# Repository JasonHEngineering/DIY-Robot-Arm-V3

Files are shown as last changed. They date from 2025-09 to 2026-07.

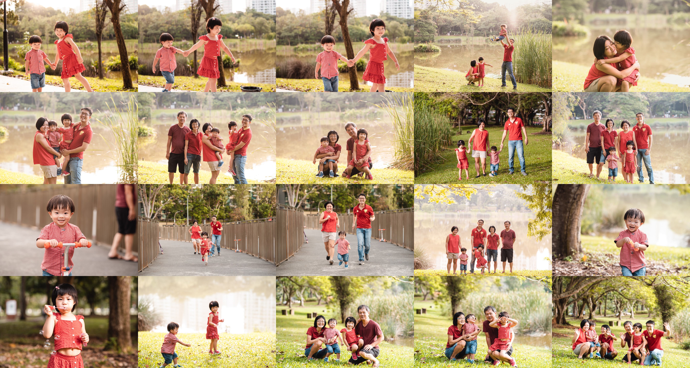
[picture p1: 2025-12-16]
Raspberry Pi - Python (Plotly dash user interface/assets/result.jpg

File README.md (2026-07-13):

# DIY-Robot-Arm-V3 

Introduction - https://youtu.be/GQhKxkShxAY

cover_page

CAD gif

# Parts Cost Estimation (SGD)

| Parts | Est. Cost (SGD) | Link |
|---|---:|---|
| CNC parts (including shipping cost) | 740 | [CAD file in GitHub](https://github.com/JasonHEngineering/DIY-Robot-Arm-V3/tree/main/CAD%20(2d%20%2B%20step%20files)) |
| 3d printed parts (including shipping cost) | 69 | [CAD file in GitHub](https://github.com/JasonHEngineering/DIY-Robot-Arm-V3/tree/main/CAD%20(2d%20%2B%20step%20files)) |
| Main PCBA (5x, including SMD assembly & shipping cost) | 158 | [Design files in GitHub](https://github.com/JasonHEngineering/DIY-Robot-Arm-V3/tree/main/PCBA%20(schema%2C%20gerbers%2C%20kicad%20project)) |
| Encoder PCBA (10x, including SMD assembly & shipping cost) | 132 | [Design files in GitHub](https://github.com/JasonHEngineering/DIY-Robot-Arm-V3/tree/main/PCBA%20(schema%2C%20gerbers%2C%20kicad%20project)) |
| Bearing 6805 2RS (25x37x7mm) (3x) | 16.07 | [AliExpress](https://s.click.aliexpress.com/e/_c33xzexj) |
| Bearing lock nut M24x1.5x30x5 (3x) | 6.24 | [AliExpress](https://s.click.aliexpress.com/e/_c3OO3rFf) |
| M3 set screw with nylon head | 4.84 | [AliExpress](https://s.click.aliexpress.com/e/_c3lDO1O5) |
| Pulley (Bore 8mm, belt width 6 mm, 2GT-30T) | 4.48 | [AliExpress](https://s.click.aliexpress.com/e/_c4LLe4XL) |
| Pulley (Bore 12mm, belt width 6 mm, 2GT-30T) | 3.06 | [AliExpress](https://s.click.aliexpress.com/e/_c3QfG9gt) |
| Timing belt (2GT-200-6mm) | 1.02 | [AliExpress](https://s.click.aliexpress.com/e/_c4KhaszX) |
| Diametric Magnets for encoders (10 pcs / lot) | 3.68 | [AliExpress](https://s.click.aliexpress.com/e/_c3Axm1QN) |
| FFC cables (pitch 0.5 mm) | 6.00 | [AliExpress](https://s.click.aliexpress.com/e/_c4SXa38p) |
| Stepper motor cables (XH2.54) | 10.00 | [AliExpress](https://s.click.aliexpress.com/e/_c3dAdb65) |
| Stepper motor 60mm model 17CS07A-180 (2x) | 38.64 | [AliExpress](https://s.click.aliexpress.com/e/_c2yzH5rf) |
| Stepper motor 60mm model 17HS4023 (3x) | 25.29 | [AliExpress](https://s.click.aliexpress.com/e/_c4bld957) |
| Stepper motor 60mm model 17HS3401S-SZ (1x) | 12.29 | [AliExpress](https://s.click.aliexpress.com/e/_c31tJidB) |
| X17-30A harmonic reducer (30:1) (5x) | 338.00 | [AliExpress](https://s.click.aliexpress.com/e/_c3xNHvpT) |
| Raspberry Pi 4B, 4GB | 160.00 | [AliExpress](https://s.click.aliexpress.com/e/_c45i6ECJ) |
| ESP32-S3-DevKitC-1 (n16r8) | 14.63 | [AliExpress](https://s.click.aliexpress.com/e/_c41bdQlh) |
| Pins & connectors (22 pins) | 1.91 | [AliExpress](https://s.click.aliexpress.com/e/_c3fCAogH) |
| TMC2209 V1.3 motor drivers (6x) | 24.13 | [AliExpress](https://s.click.aliexpress.com/e/_c4b6KFWH) |
| 24V fan (60x60x15mm) | 2.89 | [AliExpress](https://s.click.aliexpress.com/e/_c3T1QZcp) |
| E-Stop Button | 4.15 | [AliExpress](https://s.click.aliexpress.com/e/_c3gcdvel) |
| DOIT ESP32 DEV KIT V1 | 7.27 | [AliExpress](https://s.click.aliexpress.com/e/_c3el80wp) |
| PS controller | 13.34 | [AliExpress](https://s.click.aliexpress.com/e/_c4OqUEGd) |
| Mini-560-Pro (Mini Pro 5V, 3A for Raspberry Pi) | 1.51 | [AliExpress](https://s.click.aliexpress.com/e/_c37WkxiV) |
| Optical Experiment Plate 5052 Aluminum 280x320x8mm | 71.25 | [AliExpress](https://s.click.aliexpress.com/e/_c3tvnmLj) |
| Servo Claw | 26.26 | [AliExpress](https://s.click.aliexpress.com/e/_c3I3E3Mh) |
| Servo motor MG996R | 6.74 | [AliExpress](https://s.click.aliexpress.com/e/_c3sTutbP) |
| Standoffs, clamps, dowel pins | 10.00 | |
| Fasteners | 10.00 | |

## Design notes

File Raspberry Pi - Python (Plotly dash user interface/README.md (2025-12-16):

# User Interface hosted in Raspberry Pi 3/4 (Work in progress)

Plotly Dash App - written in Python. 3 main pages.

Page 1 - "Angles"
To control robotic arm by angle entries.



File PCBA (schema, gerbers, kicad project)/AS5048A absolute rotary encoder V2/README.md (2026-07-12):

# Notes 

1) Although there are 7 jumper pads here for purpose of using these encoders in series with SPI protocol, however due to GPIO0 on ESP32-S3 being a bootstrap pin, I will not be using jumper JP5 on the absolute encoder board at all. Consequently, the remaining chip select jumper for all the 6 axis encoders are allocated as shown in the table, with the soldering done accordingly.

<!-- wp:image {"id":4006,"sizeSlug":"large","linkDestination":"none"} -->

<!-- /wp:image -->

<!-- wp:image {"id":4002,"sizeSlug":"large","linkDestination":"none"} -->

<!-- /wp:image -->

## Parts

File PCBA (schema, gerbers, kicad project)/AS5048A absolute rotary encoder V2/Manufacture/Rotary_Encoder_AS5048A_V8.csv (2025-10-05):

Comment | Designator | Footprint | LCSC
GRM155R60J106ME15D | C1 | 10uF_cap_GRM155R60J106ME15D:CAPC1005X65N | C412251
GCM155R71C104KA55J | C2 | 100nf_cap_GCM155R71C104KA55J:CAPC1005X55N | C2655418
CC0603KRX7R7BB105 | C3,C4 | MLCC_16V_1uF_X7R_±10%_0603_C106248:MLCC_16V_1uF_X7R_±10%_0603_C106248 | C106248
BAT20JFILM | D1 | diode_BAT20JFILM:SOD-323 | C155590
AFC01-S12FCA-00 | FPC1,FPC2 | FFC_conn_Flip type_12P_P=0.5mm_C262661:FFC_conn_Flip type_12P_P=0.5mm_C262661 | C262661
Conn_01x01_Female | J2 | Connector_PinHeader_1.00mm:PinHeader_1x01_P1.00mm_Vertical
Jumper_2_Open | JP1,JP2,JP3,JP4,JP5,JP6,JP7 | solder_jumpers:SolderJumper-2_P1.3mm_Open_TrianglePad1.0x1.5mm
Green | LED1 | green_LED_wurth_150060GS75000_0603_C5252984:LEDC1608X80N | C5252984
0402WGD1001TCE | R1 | Resistor_62.5mW_50V_±0.5%_1kΩ_0402_C407754:Resistor_62.5mW_50V_±0.5%_1kΩ_0402_C407754 | C407754
RC0402FR-0733RL | R2 | Resistor_62.5mW_50V_±1%_33Ω_0402_C138002:Resistor_62.5mW_50V_±1%_33Ω_0402_C138002 | C138002
RC0402FR-0710KL | R3 | Resistor_62.5mW_50V_±1%_10kΩ_0402_C60490:Resistor_62.5mW_50V_±1%_10kΩ_0402_C60490 | C60490
AS5048A | U1 | Package_SO:TSSOP-14_4.4x5mm_P0.65mm | C2655181
TLV75733PDBVR | U2 | LDO_1A_Fixed_3.3V_out_5.5V_in_SOT-23-5_C485517:LDO_1A_Fixed_3.3V_out_5.5V_in_SOT-23-5_C485517 | C485517

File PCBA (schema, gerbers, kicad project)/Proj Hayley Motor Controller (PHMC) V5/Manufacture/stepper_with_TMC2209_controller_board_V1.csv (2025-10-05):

Comment | Designator | Footprint | LCSC
FS55X226K500EHG | C1,C6 | Cap_MLCC_50V_22uF_X7R_2220_C784103:Cap_MLCC_50V_22uF_X7R_2220_C784103 | C784103
CC0603KRX7R9BB104 | C2 | MLCC_Yageo_50V_100nF_X7R_±10%_0603_C14663:MLCC_Yageo_50V_100nF_X7R_±10%_0603_C14663 | C14663
470uF, 35V | C3 | 470uF_35V_Alu_cap_panasonic_EEH-ZS1V471P_C403803:CAP_EEHZS1V471P | C403803
GCM155R71C104KA55J | C4 | 100nf_cap_GCM155R71C104KA55J:CAPC1005X55N | C2655418
0.1uF, 16V | C5 | 100nf_16V_MLCC_GRM155R71C104KA88D_C71629:CAPC1005X55N | C71629
CGA2B3X7R1V104KT0Y0F | C7,C8,C11,C12,C15,C16,C19,C20 | TDK cap_100nF_35V_C0402_C343047:C0402_L1.0-W0.5-H0.5 | C343047
RVT1V101M0605 | C9,C10,C13,C14,C17,C18 | Capacitor_100uF_35V_75mA@120Hz_±20%_D6pt3xL5pt4mm_C3151830:Capacitor_100uF_35V_75mA@120Hz_±20%_D6pt3xL5pt4mm_C3151830 | C3151830
BZT52C5V6S_C19077441 | D2 | BZT52C5V6S_5.2V_to_6V_200mW_5.6V_SOD-323_Zener_Diodes_C19077441:SOD-323_L1.7-W1.3-LS2.6-RD | C19077441
0ZCJ0020FF2E | F1 | Bel_Fuse_0ZCJ0020FF2E_30V_200mA_10A_400mA_1206_Resettable_Fuses_C6964258.pretty:F1206 | C6964258
AFC01-S12FCA-00 | FPC1 | FFC_conn_Flip type_12P_P=0.5mm_C262661:FFC_conn_Flip type_12P_P=0.5mm_C262661 | C262661
FTC252012S100MBCA | L1 | Inductor_10uH_1pt6A_2x2pt5mm_C5832376:Inductor_10uH_1pt6A_2x2pt5mm_C5832376 | C5832376
Green | LED1 | green_LED_wurth_150060GS75000_0603_C5252984:LEDC1608X80N | C5252984
MAC97A8-23-3L | Q1 | KY_MAC97A8-23-3L_10mA_800V_SOT-23-3L_Thyristors_SCR_C2831929:SOT-23-3_L2.9-W1.6-P1.90-LS2.8-BL-A | C2831929
5kR, 0.25W | R1,R33,R34 | 5kR_250mW_yageo_RT1206BRD075KL_1206_C870818:RESC3116X65N | C870818
10kR, 100mW | R2 | 10kR_100mW_yageo_RC0603FR-0710KL_0603_C98220:RESC1607X60N | C98220
1kR, 0.25W | R20,R21 | 1kR_250mW_yageo_RC1206FR-071KL_1206_C131398:RESC3116X65N | C131398
RC0402FR-07100KL | R3,R4,R8,R15,R16,R17,R18,R19 | Resistor_ 100kΩ_62.5mW_50V_0402_C60491:Resistor_ 100kΩ_62.5mW_50V_0402_C60491 | C60491
FRC0805F1902TS | R5 | Resistor_19kΩ_0.125W_150V_0805_C2930177:Resistor_19kΩ_0.125W_150V_0805_C2930177 | C2930177
33R, 0.1W | R6,R7,R26,R27,R28,R29,R30,R31,R32 | 33R_100mW_yageo_RC0603JR-0733RL_0603_C108407:RESC1608X55N | C108407
0402WGF2000TCE | R9,R10,R11,R12,R13,R14 | 62.5mW_Resistor_50V_±1%_200Ω_0402_C25087:R0402 | C25087
DSWB06LHGET | SW1 | 6_SPST_Through_Hole_DIP_C99416:6_SPST_Through_Hole_DIP_C99416 | C99416
TP6841S6-A | U1 | Step-down_800mA_4.5V_to_40V_SOT-23-6_C2844924:SOT-23-6_L2.9-W1.6-P0.95-LS2.8-BL | C2844924
XL-1608UBC-06A | U2,U5,U6,U7,U8,U9,U10 | Blue_LED_5mA_456nm~476nm_130°_2.6V~3V_0603_C7371904:Blue_LED_5mA_456nm~476nm_130°_2.6V~3V_0603_C7371904 | C7371904
XT30UPB-M | U4 | high_current_connector_amass_XT30UPB-M_C108769:XT30UPB-M | C108769

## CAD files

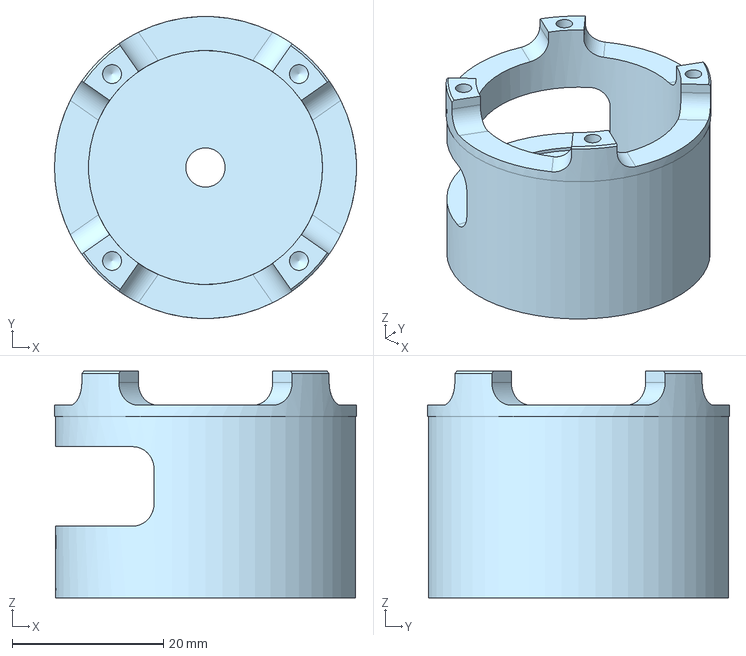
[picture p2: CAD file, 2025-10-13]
CAD (2d + step files)/Step Files/Part Studio 51.step
40.0 x 40.0 x 30.0 mm

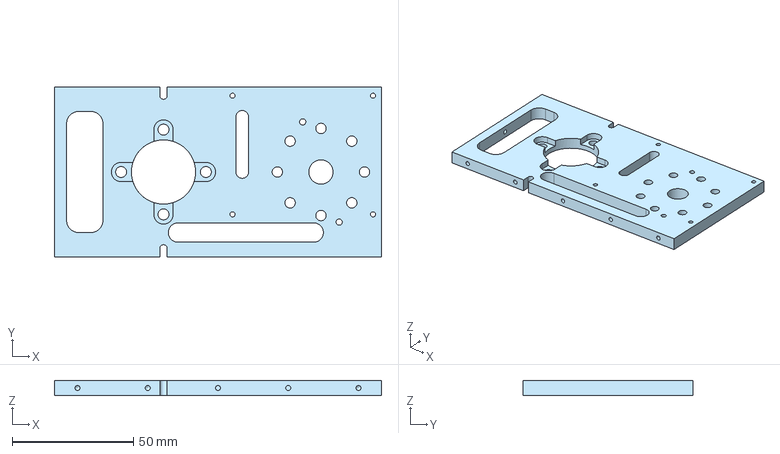
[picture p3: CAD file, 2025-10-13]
CAD (2d + step files)/Step Files/Part Studio 52.step
135.0 x 70.0 x 6.00 mm

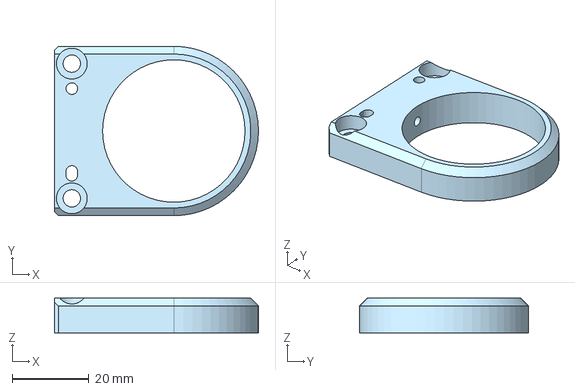
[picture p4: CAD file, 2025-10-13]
CAD (2d + step files)/Step Files/Part Studio 42.step
53.0 x 44.0 x 9.00 mm

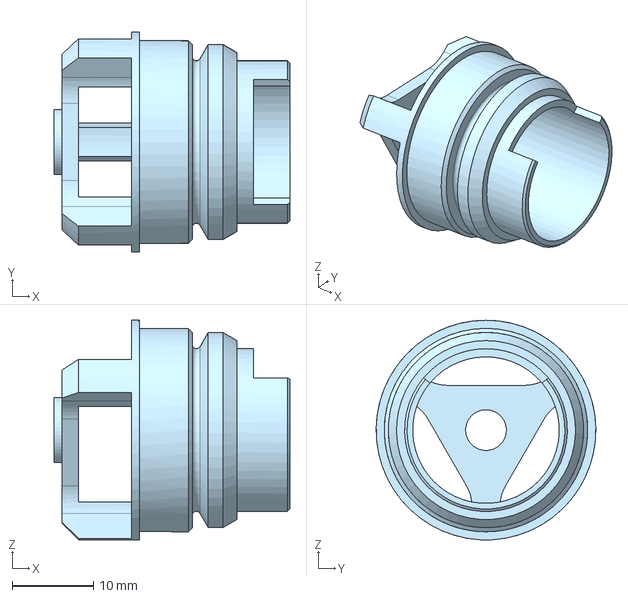
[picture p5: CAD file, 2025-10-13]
CAD (2d + step files)/Step Files/Part Studio 29.step
29.0 x 27.0 x 27.0 mm

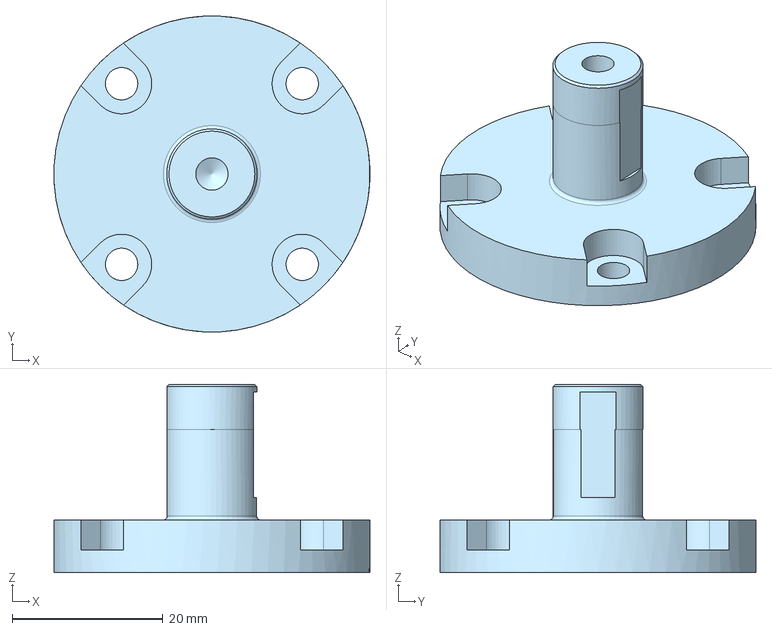
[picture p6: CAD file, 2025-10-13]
CAD (2d + step files)/Step Files/Part Studio 49.step
42.0 x 42.0 x 25.0 mm

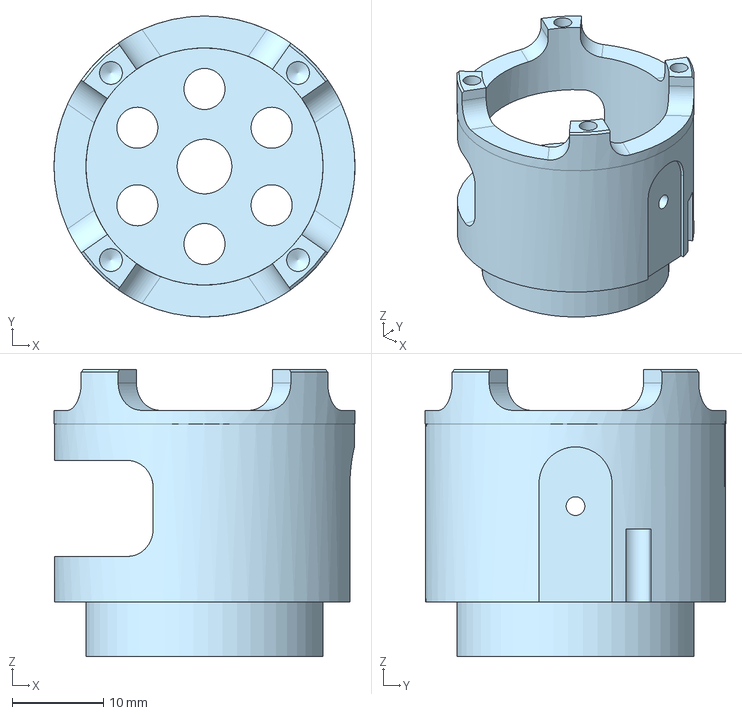
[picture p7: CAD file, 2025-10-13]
CAD (2d + step files)/Step Files/Part Studio 36.step
33.0 x 33.0 x 31.5 mm

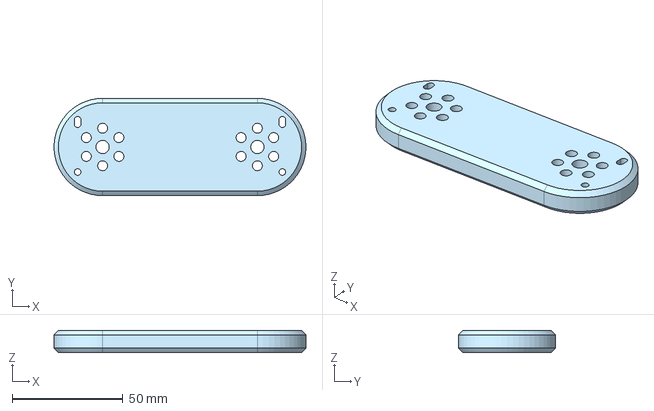
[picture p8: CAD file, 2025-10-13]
CAD (2d + step files)/Step Files/Part Studio 45.step
114.0 x 44.0 x 10.0 mm

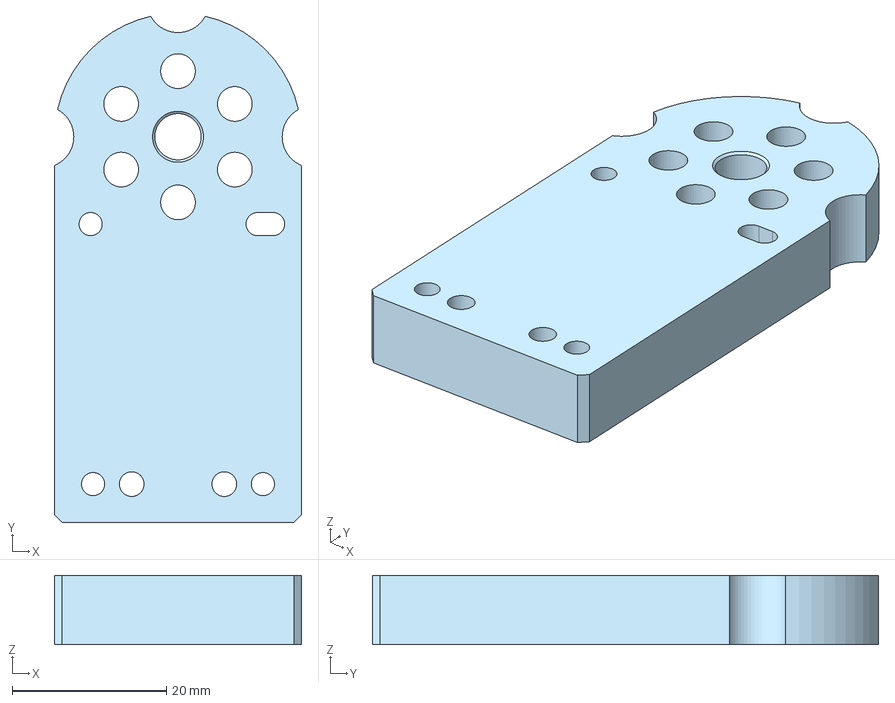
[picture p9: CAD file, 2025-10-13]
CAD (2d + step files)/Step Files/Part Studio 34.step
32.0 x 65.6 x 9.00 mm

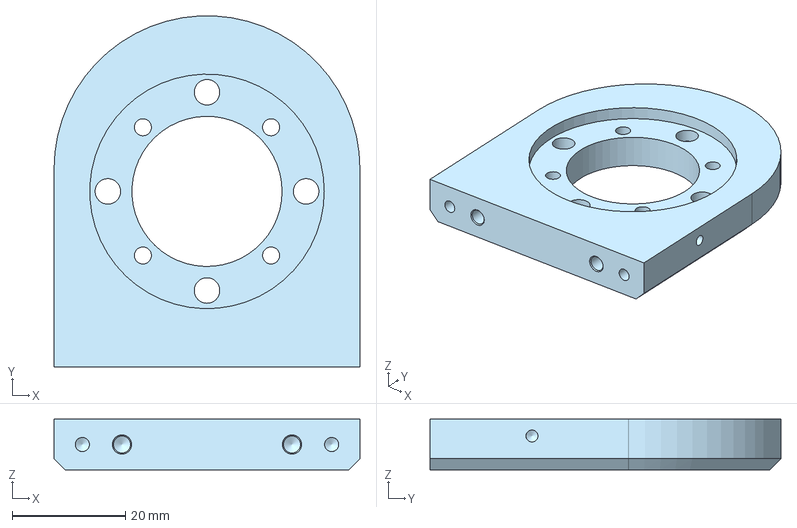
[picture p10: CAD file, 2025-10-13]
CAD (2d + step files)/Step Files/Part Studio 31.step
54.0 x 62.0 x 9.00 mm

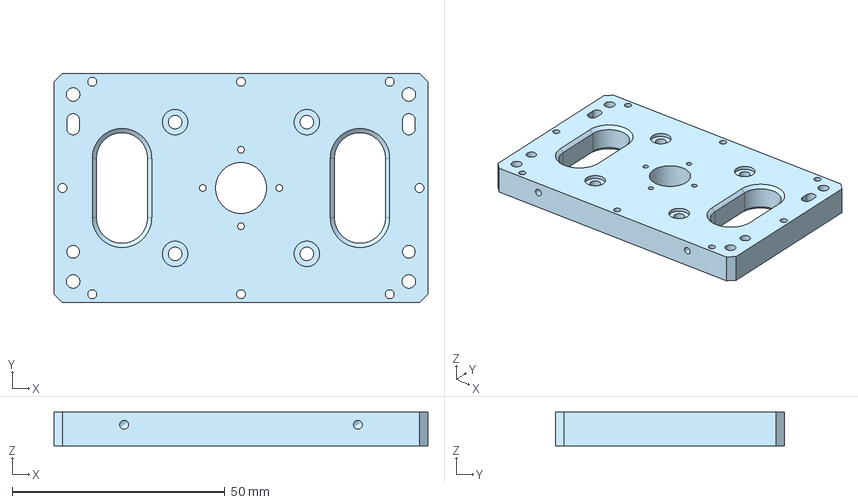
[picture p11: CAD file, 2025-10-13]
CAD (2d + step files)/Step Files/Part Studio 30.step
88.0 x 54.0 x 8.00 mm

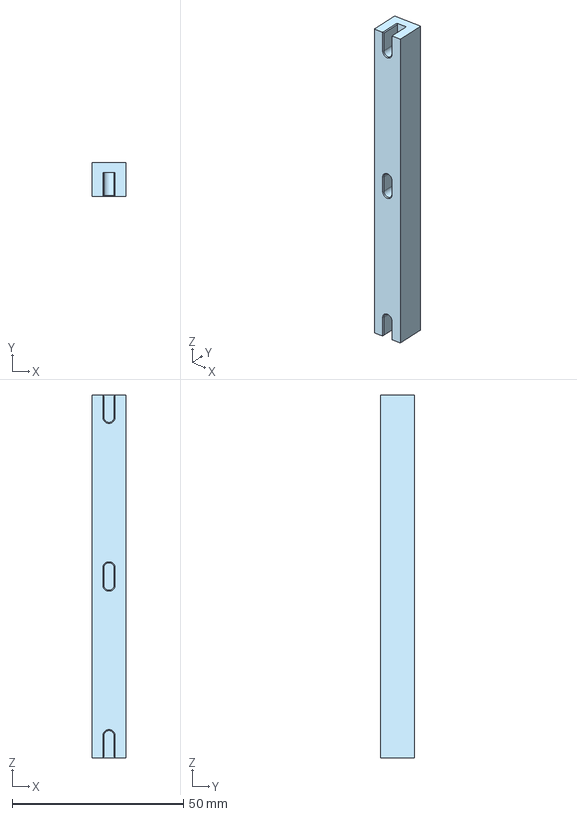
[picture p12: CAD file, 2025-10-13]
CAD (2d + step files)/Step Files/cal_tool_1.step
10.0 x 10.0 x 106.0 mm

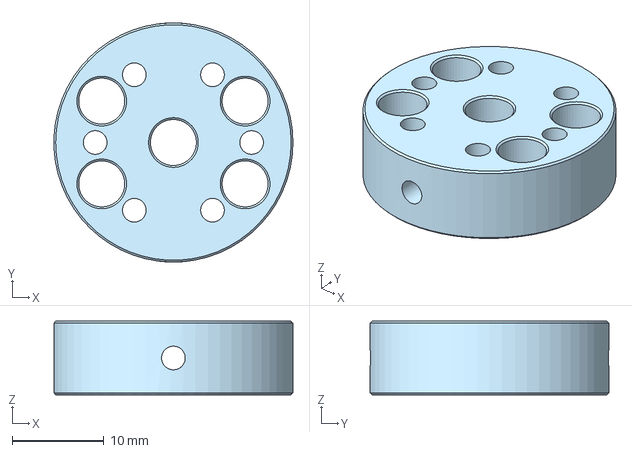
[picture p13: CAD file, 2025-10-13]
CAD (2d + step files)/Step Files/Part Studio 55.step
26.0 x 26.0 x 8.00 mm

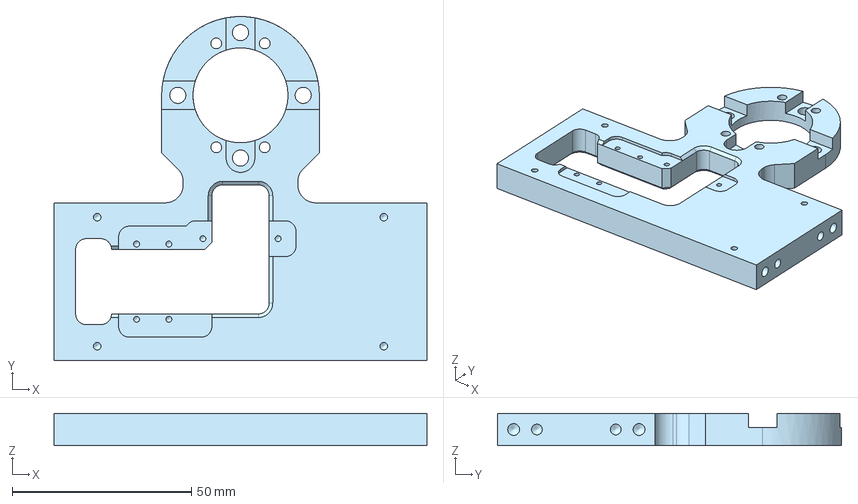
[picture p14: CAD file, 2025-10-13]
CAD (2d + step files)/Step Files/Part Studio 41.step
104.0 x 96.0 x 9.00 mm

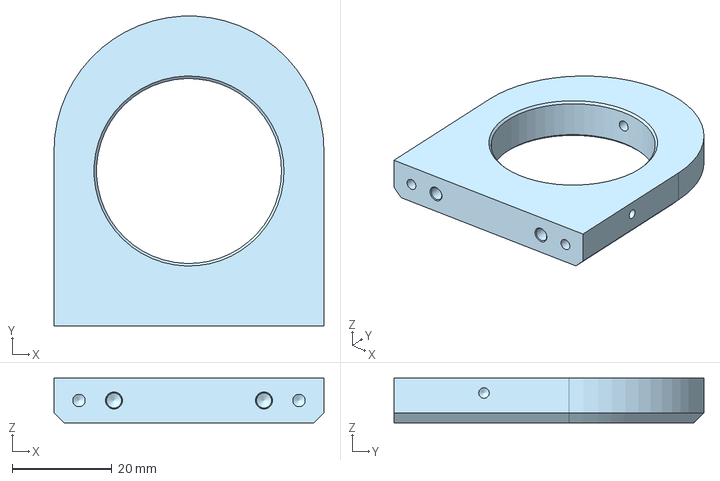
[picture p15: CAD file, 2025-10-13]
CAD (2d + step files)/Step Files/Part Studio 32.step
54.0 x 62.0 x 9.00 mm

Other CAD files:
CAD (2d + step files)/Step Files/Part Studio 40.step
CAD (2d + step files)/Step Files/Part Studio 28.step
CAD (2d + step files)/Step Files/Part Studio 50.step
CAD (2d + step files)/Step Files/Part Studio 53.step
CAD (2d + step files)/Step Files/Part Studio 23.step
CAD (2d + step files)/Step Files/Part Studio 33.step
CAD (2d + step files)/Step Files/Part Studio 35.step
CAD (2d + step files)/Step Files/Part Studio 39.step
CAD (2d + step files)/Step Files/Part Studio 44.step
CAD (2d + step files)/Step Files/Part Studio 48.step

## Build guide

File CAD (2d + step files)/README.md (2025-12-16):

# CAD: Step files & 2d detail 







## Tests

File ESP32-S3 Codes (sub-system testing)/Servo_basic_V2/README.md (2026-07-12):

# Servo mechanism basic sanity check

Code to sanity test if the Servo mechanism is working. 
PWM pin used from ESP32-S3 is now GPIO38 (although it was originally with GPIO 43, which is not suitable due to Serial com)
Servo in this case was a MG996R, wired with an independent 5V source (I was using a Mini 560 PRO).

<!-- wp:image {"id":4318,"sizeSlug":"large","linkDestination":"none"} -->

<!-- /wp:image -->

Wiring colours for MG996R:

Yellow - PWM signal 

Red    - 5 to 6 V

Brown  - Ground

Preview:

servo gif

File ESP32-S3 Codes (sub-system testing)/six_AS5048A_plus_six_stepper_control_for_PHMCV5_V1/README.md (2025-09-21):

# six_AS5048A_plus_six_stepper_control_for_PHMCV5_V1

Code to sanity test if the controller board with TMC2209 motor driver and a single encoder attached are working.
Stepper motor drives forward and backward by 500 steps each time and repeatedly. Absolute encoder takes absolute reading at the end of each direction before stepper switch direction again.

Setup as shown:

# Integrated stepper motors (Nema 17) and encoders (AS5048A)

6DOF_jogging_and_read_encoders -gif

# Stepper motors Stepping and Direction pins



# Absolute Encoders jumper settings and pins



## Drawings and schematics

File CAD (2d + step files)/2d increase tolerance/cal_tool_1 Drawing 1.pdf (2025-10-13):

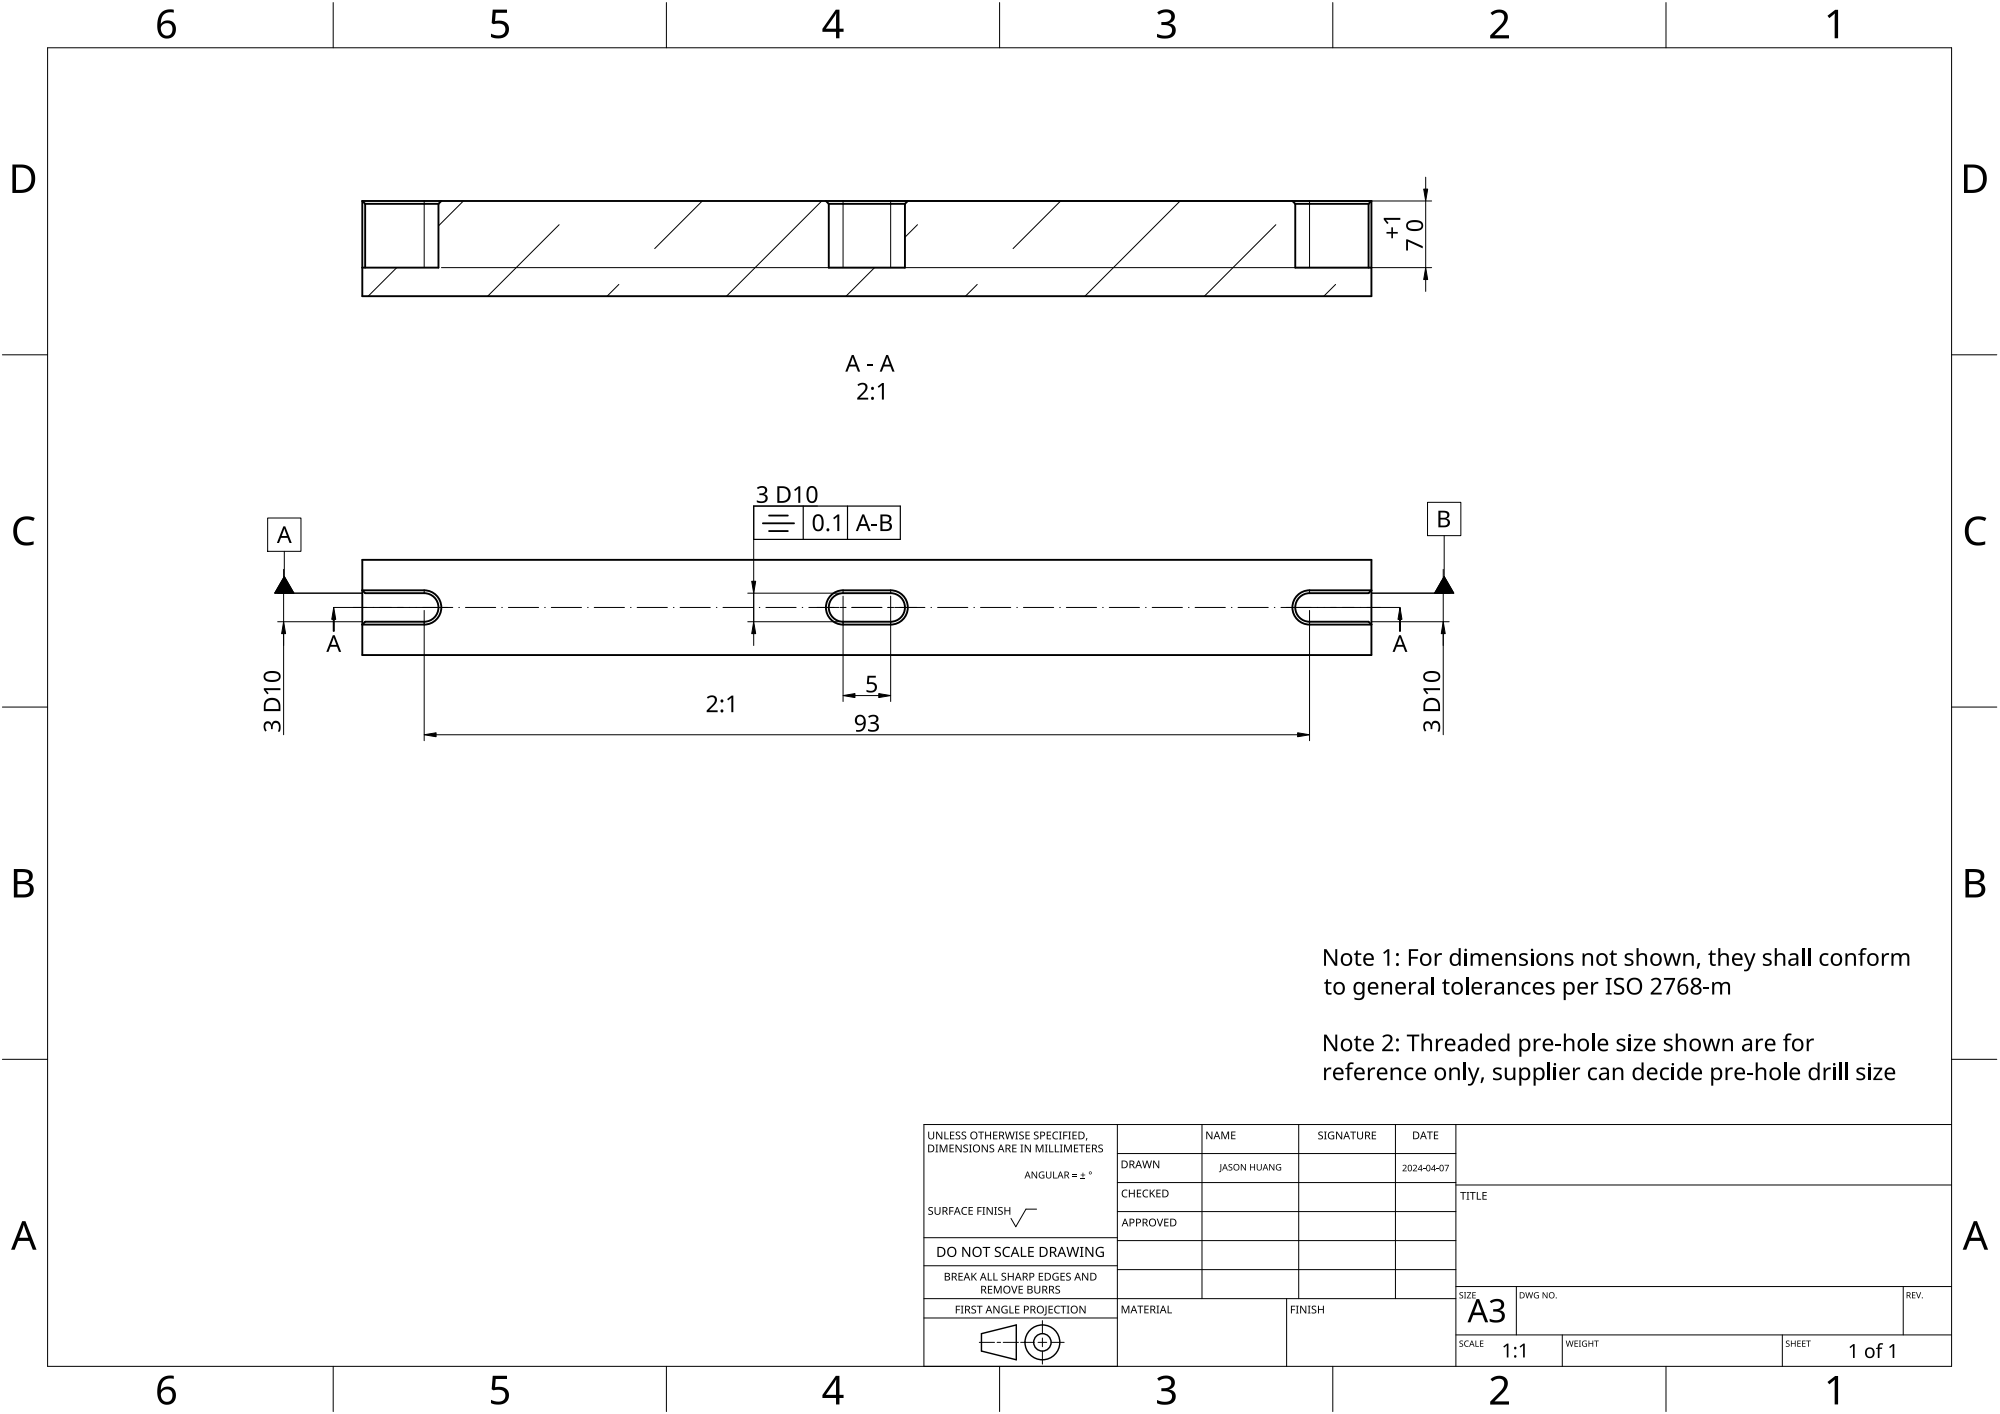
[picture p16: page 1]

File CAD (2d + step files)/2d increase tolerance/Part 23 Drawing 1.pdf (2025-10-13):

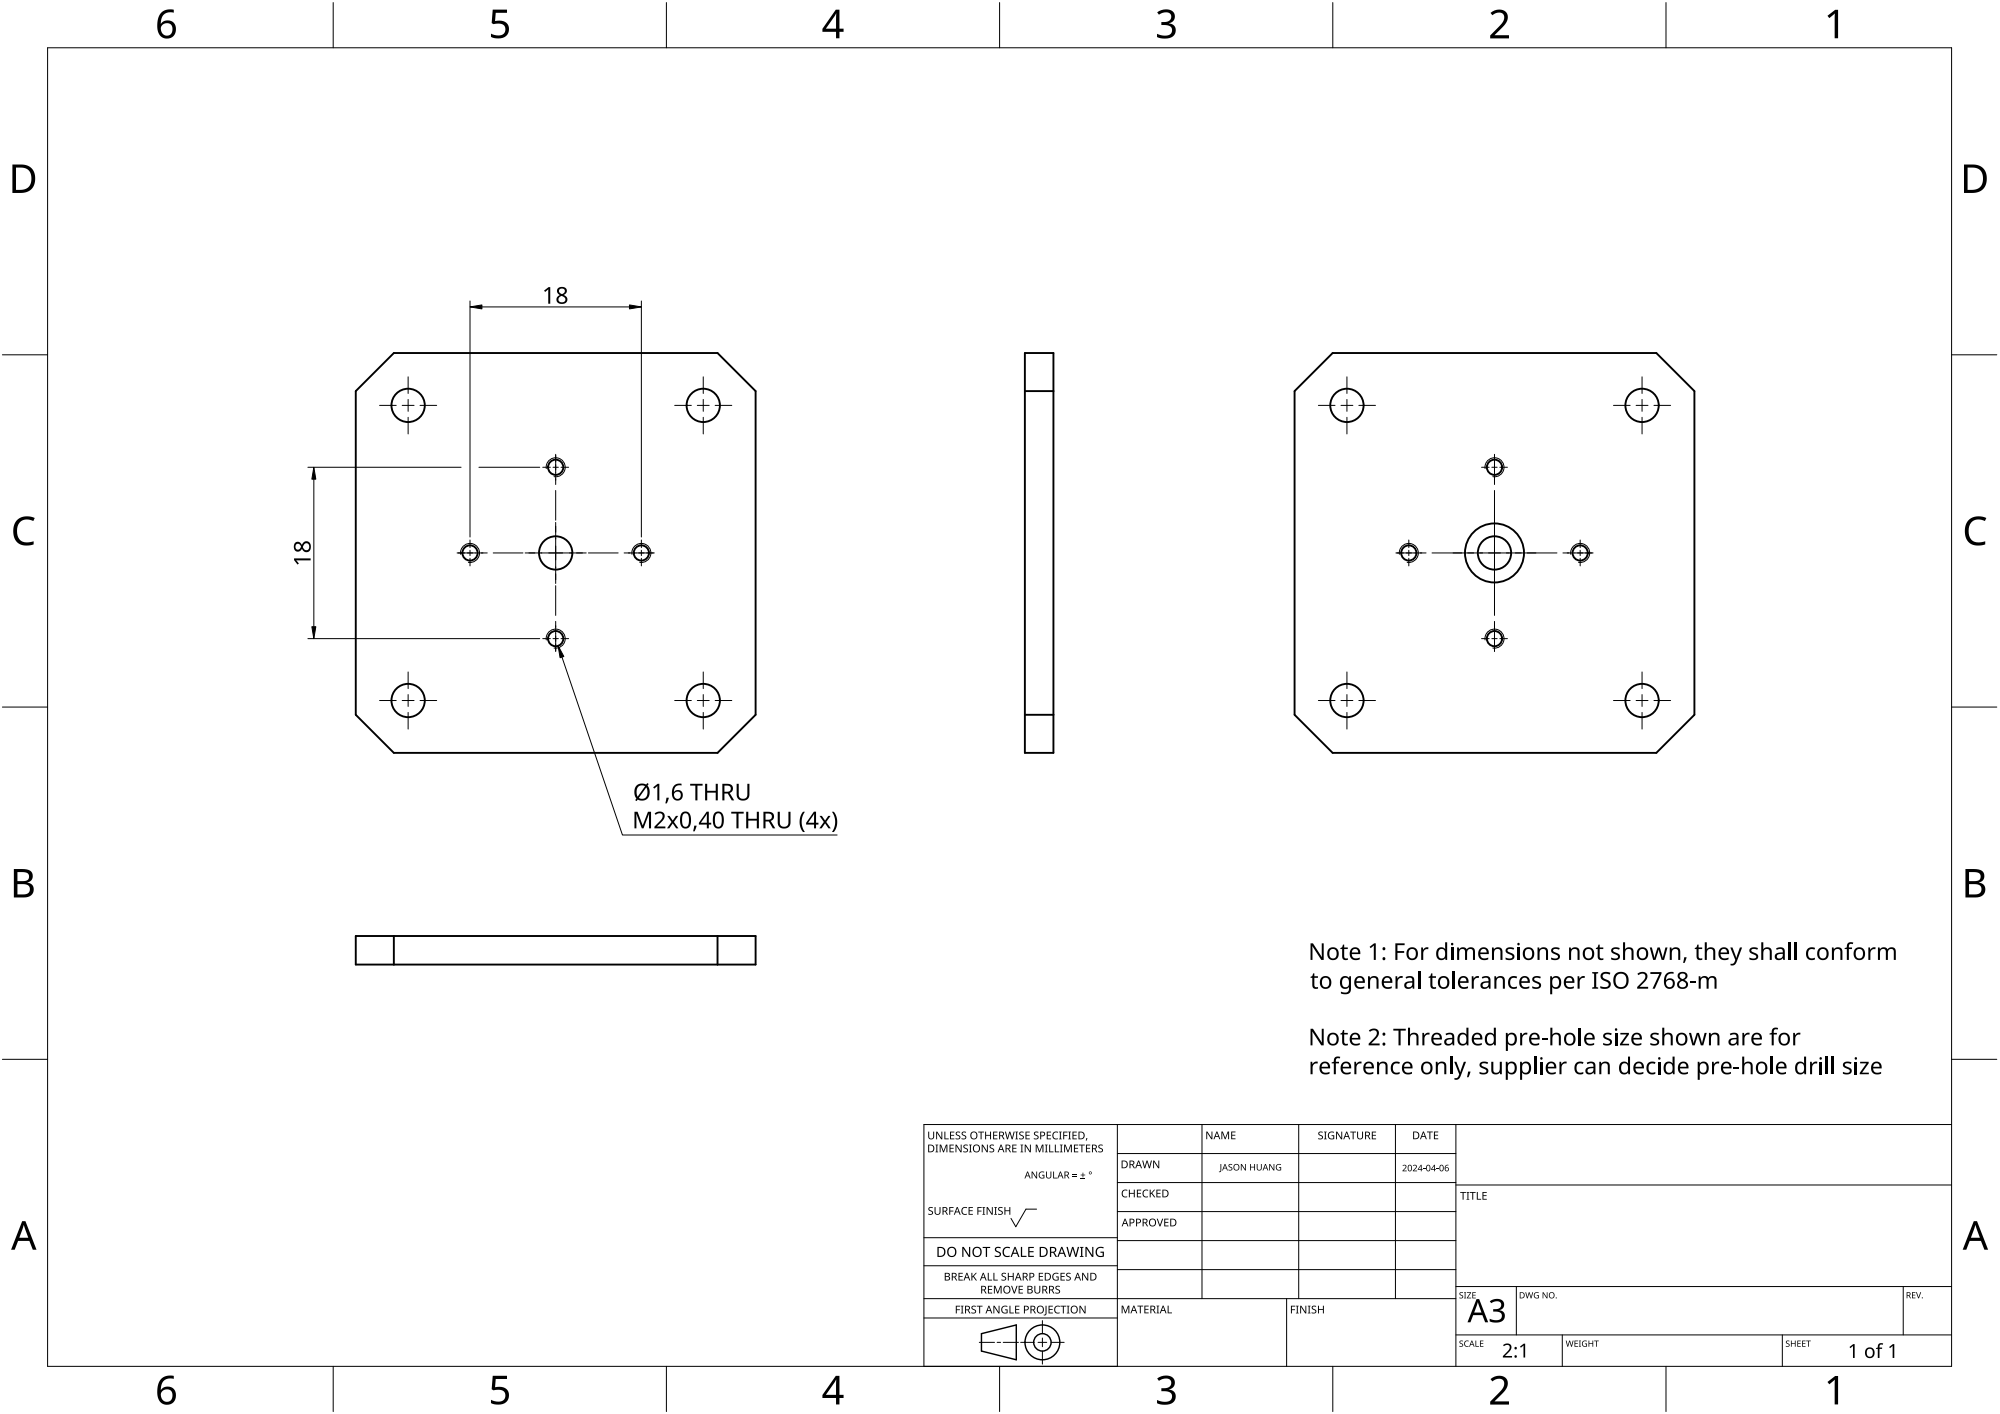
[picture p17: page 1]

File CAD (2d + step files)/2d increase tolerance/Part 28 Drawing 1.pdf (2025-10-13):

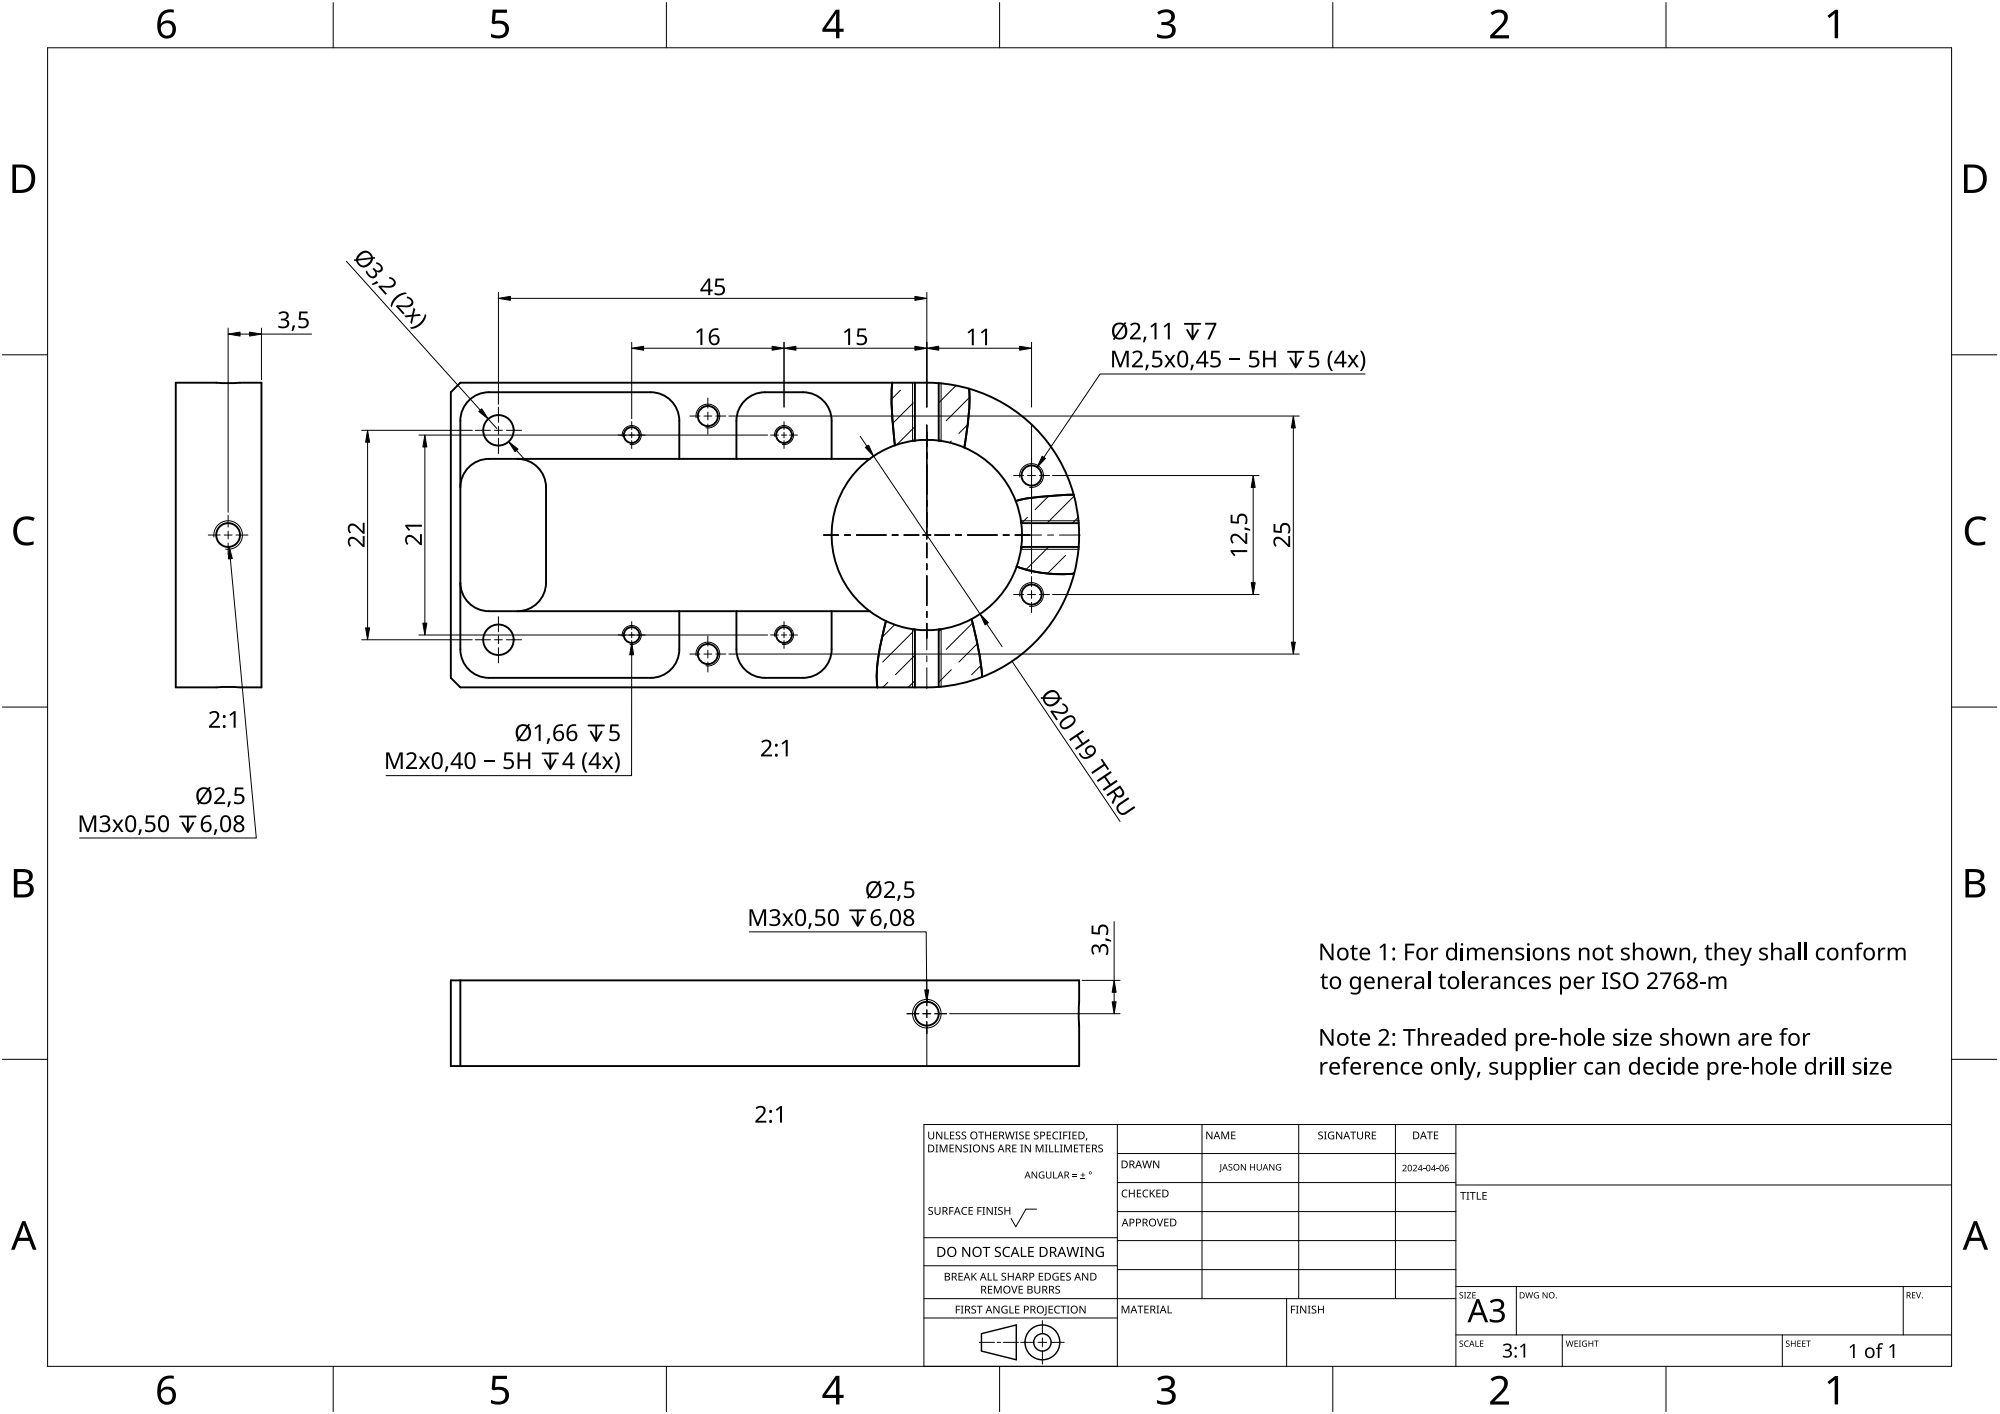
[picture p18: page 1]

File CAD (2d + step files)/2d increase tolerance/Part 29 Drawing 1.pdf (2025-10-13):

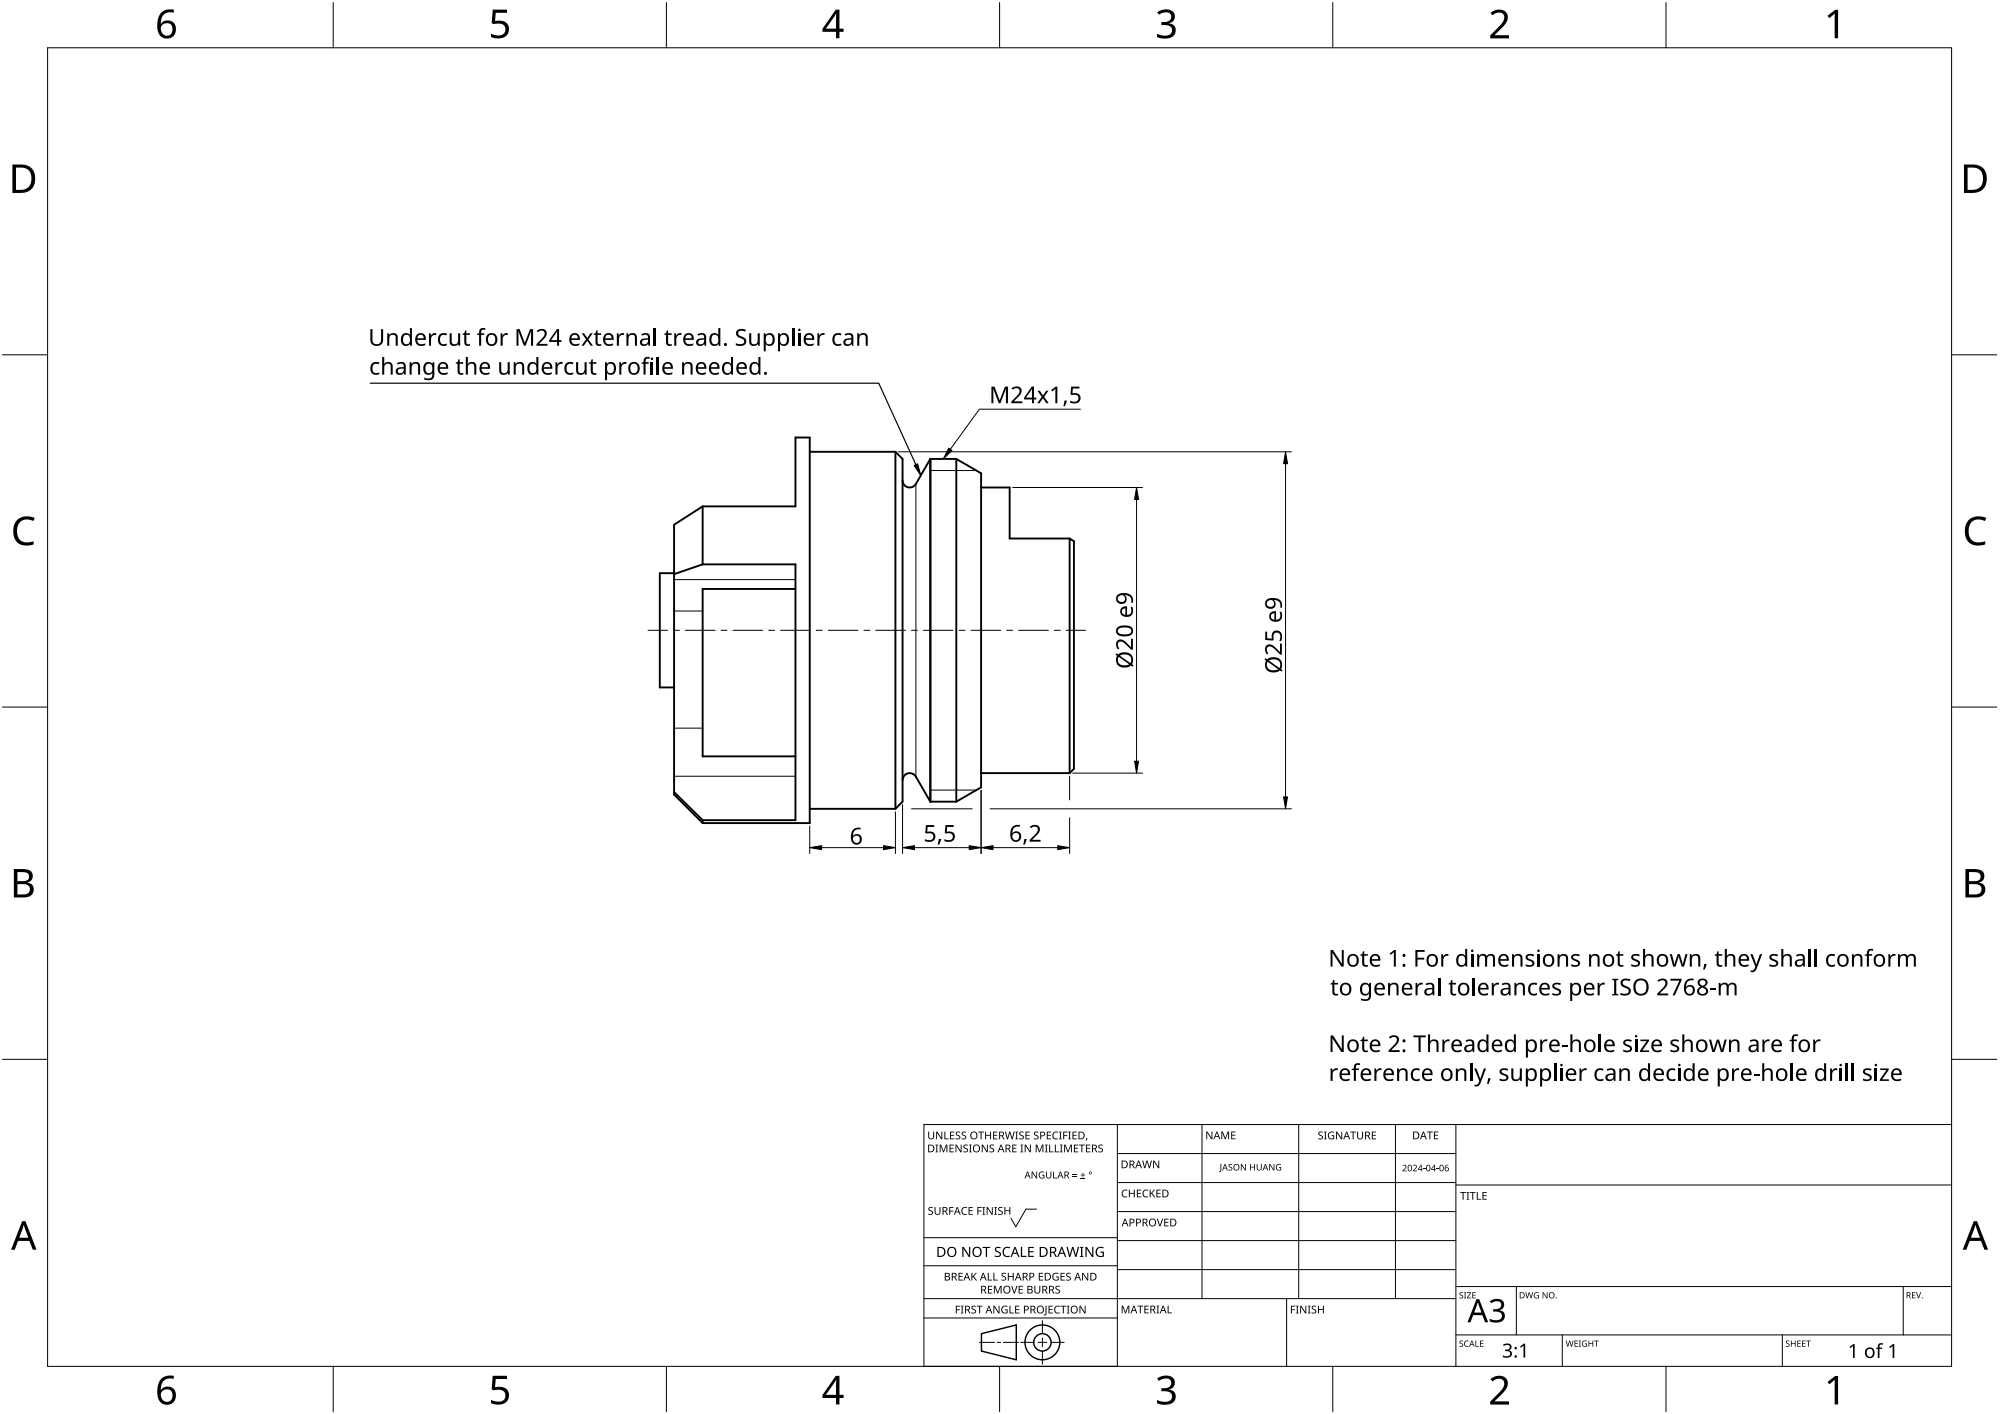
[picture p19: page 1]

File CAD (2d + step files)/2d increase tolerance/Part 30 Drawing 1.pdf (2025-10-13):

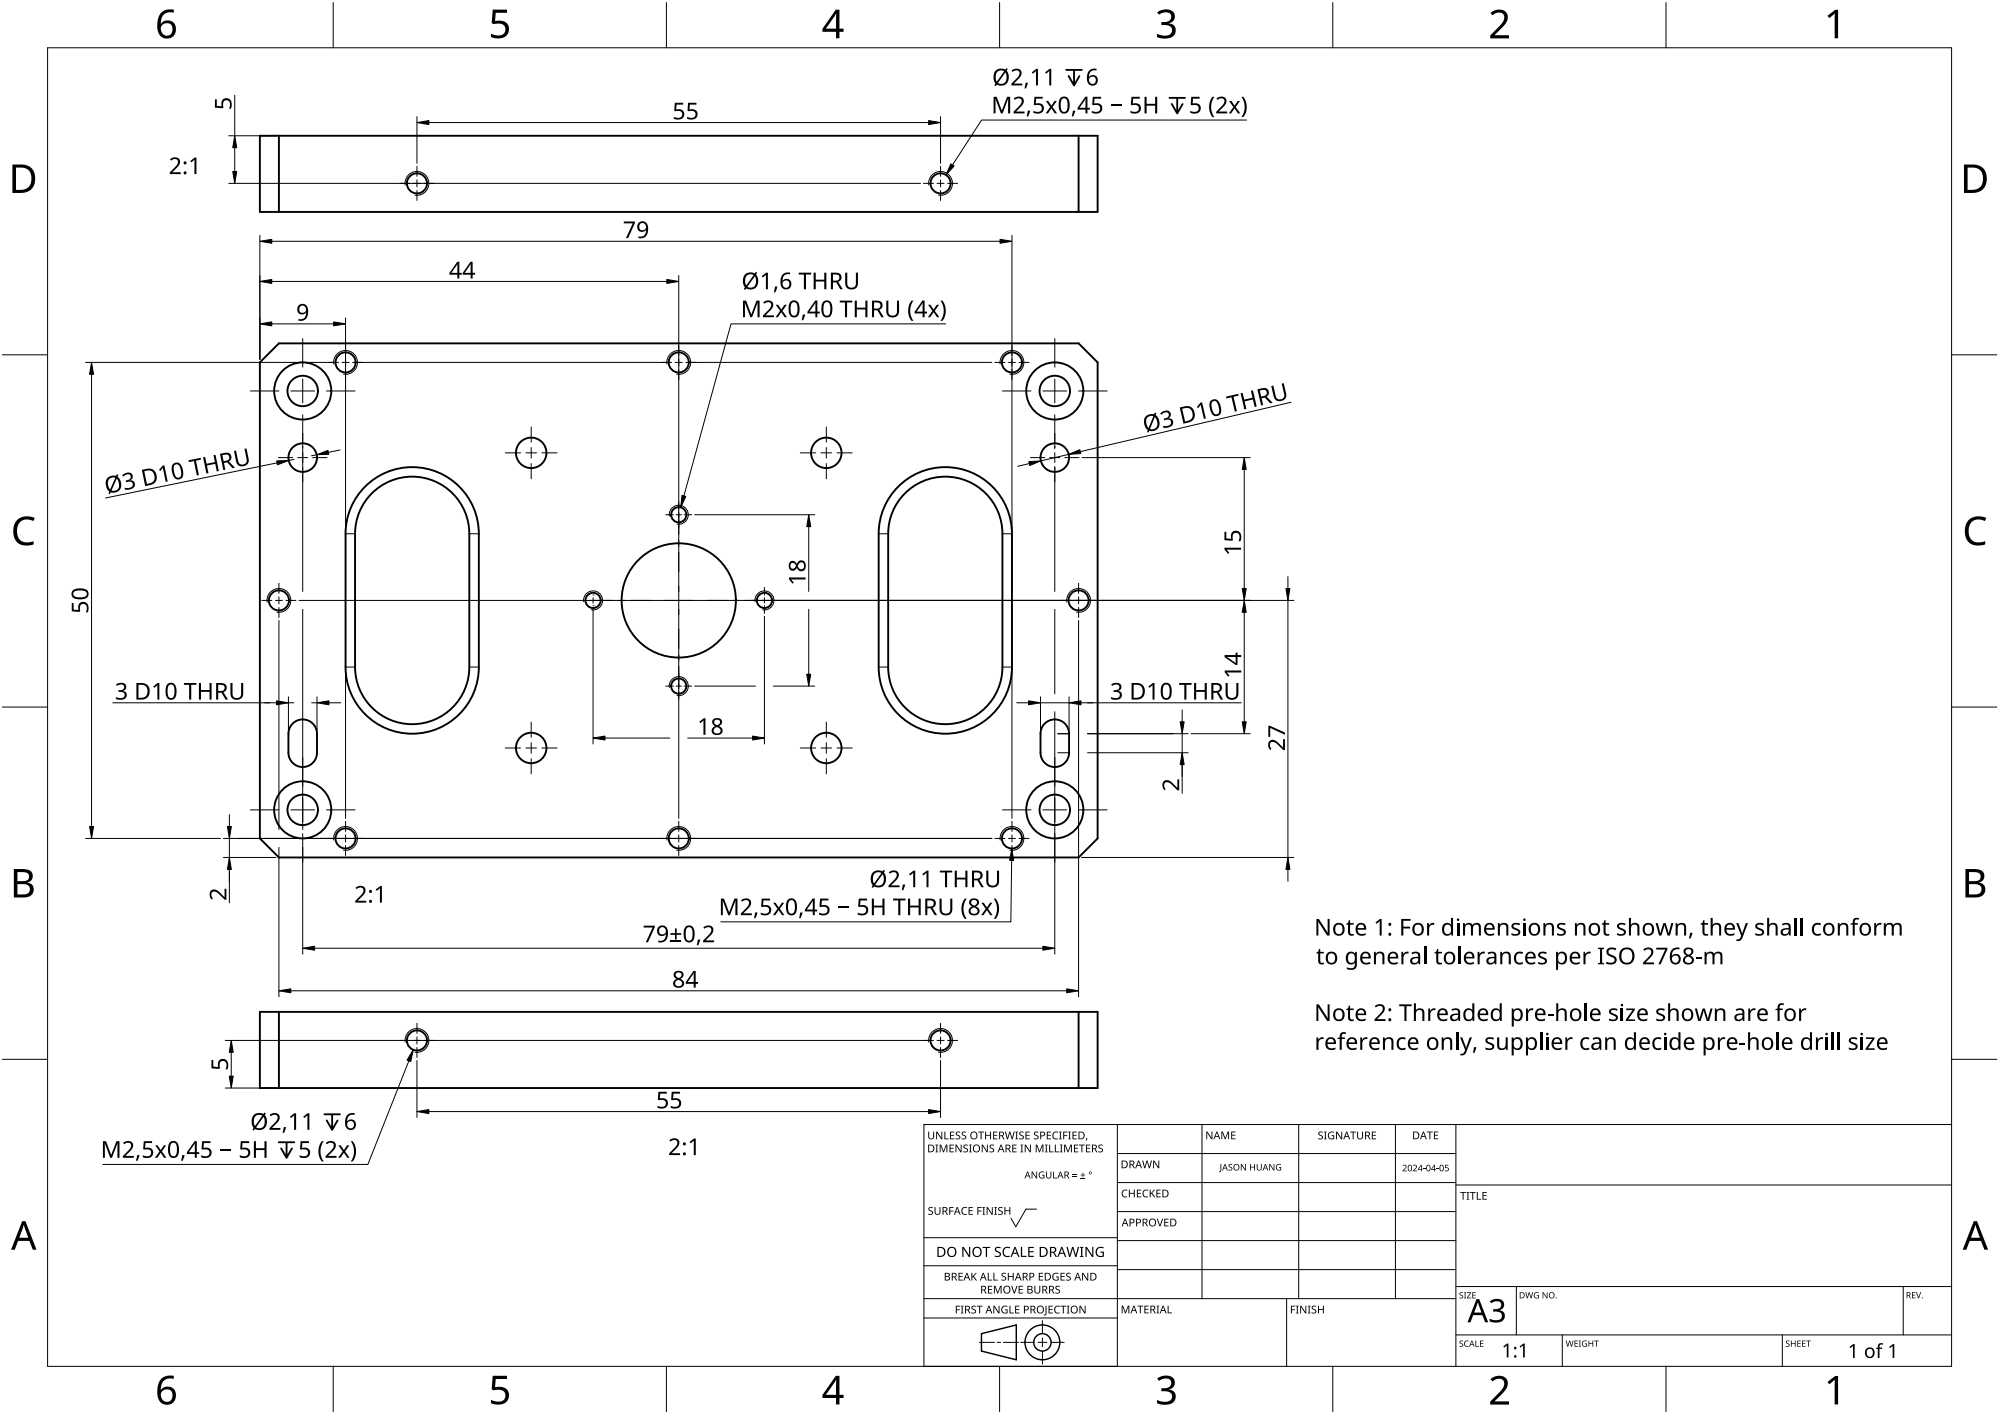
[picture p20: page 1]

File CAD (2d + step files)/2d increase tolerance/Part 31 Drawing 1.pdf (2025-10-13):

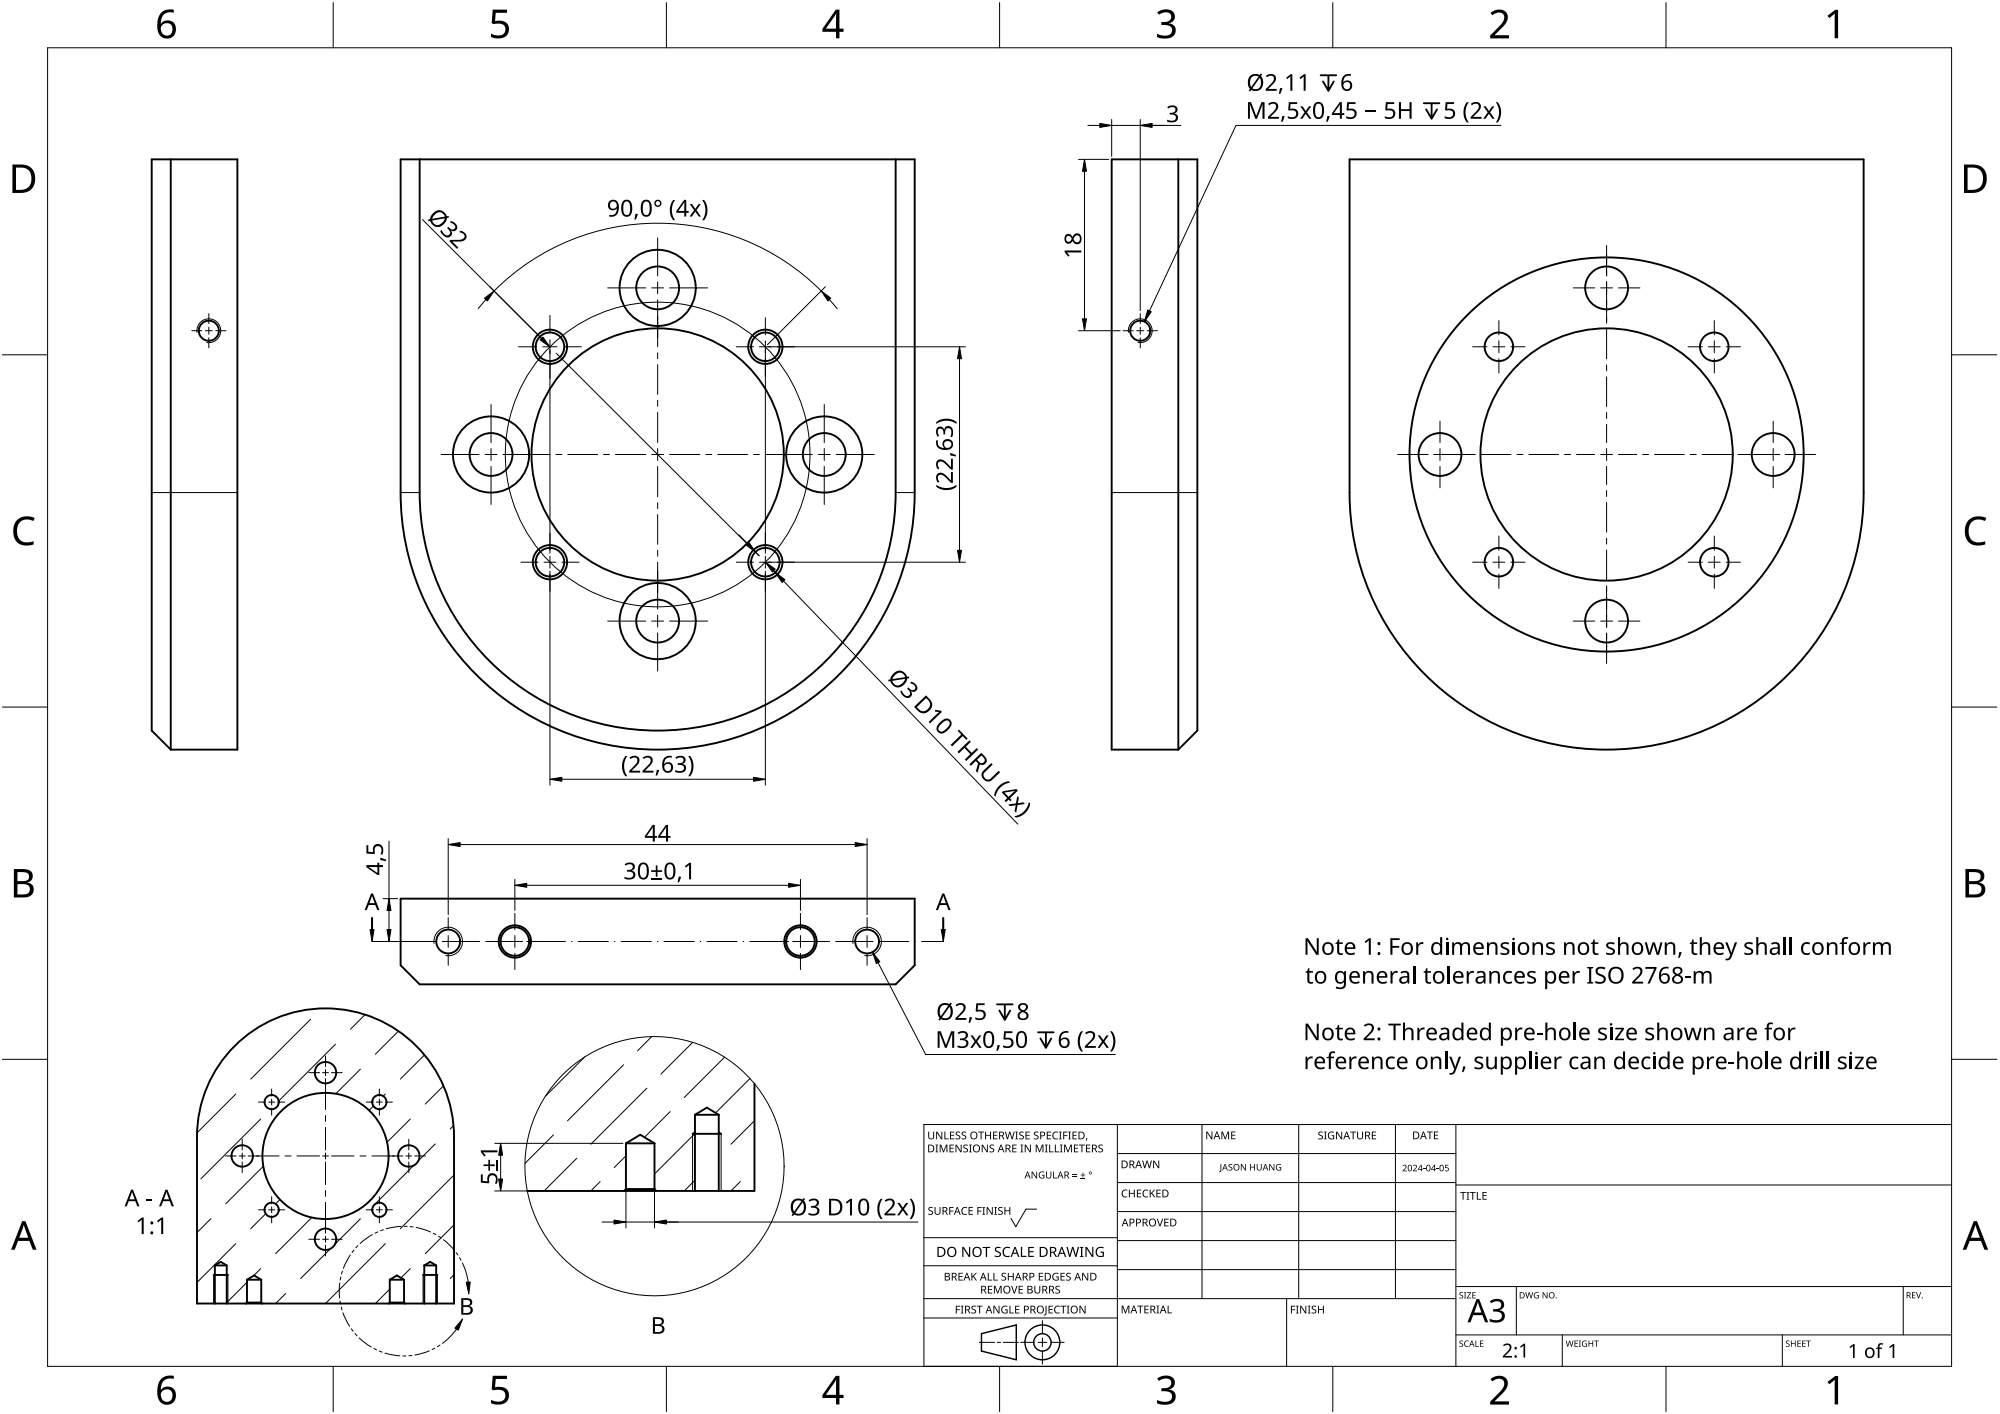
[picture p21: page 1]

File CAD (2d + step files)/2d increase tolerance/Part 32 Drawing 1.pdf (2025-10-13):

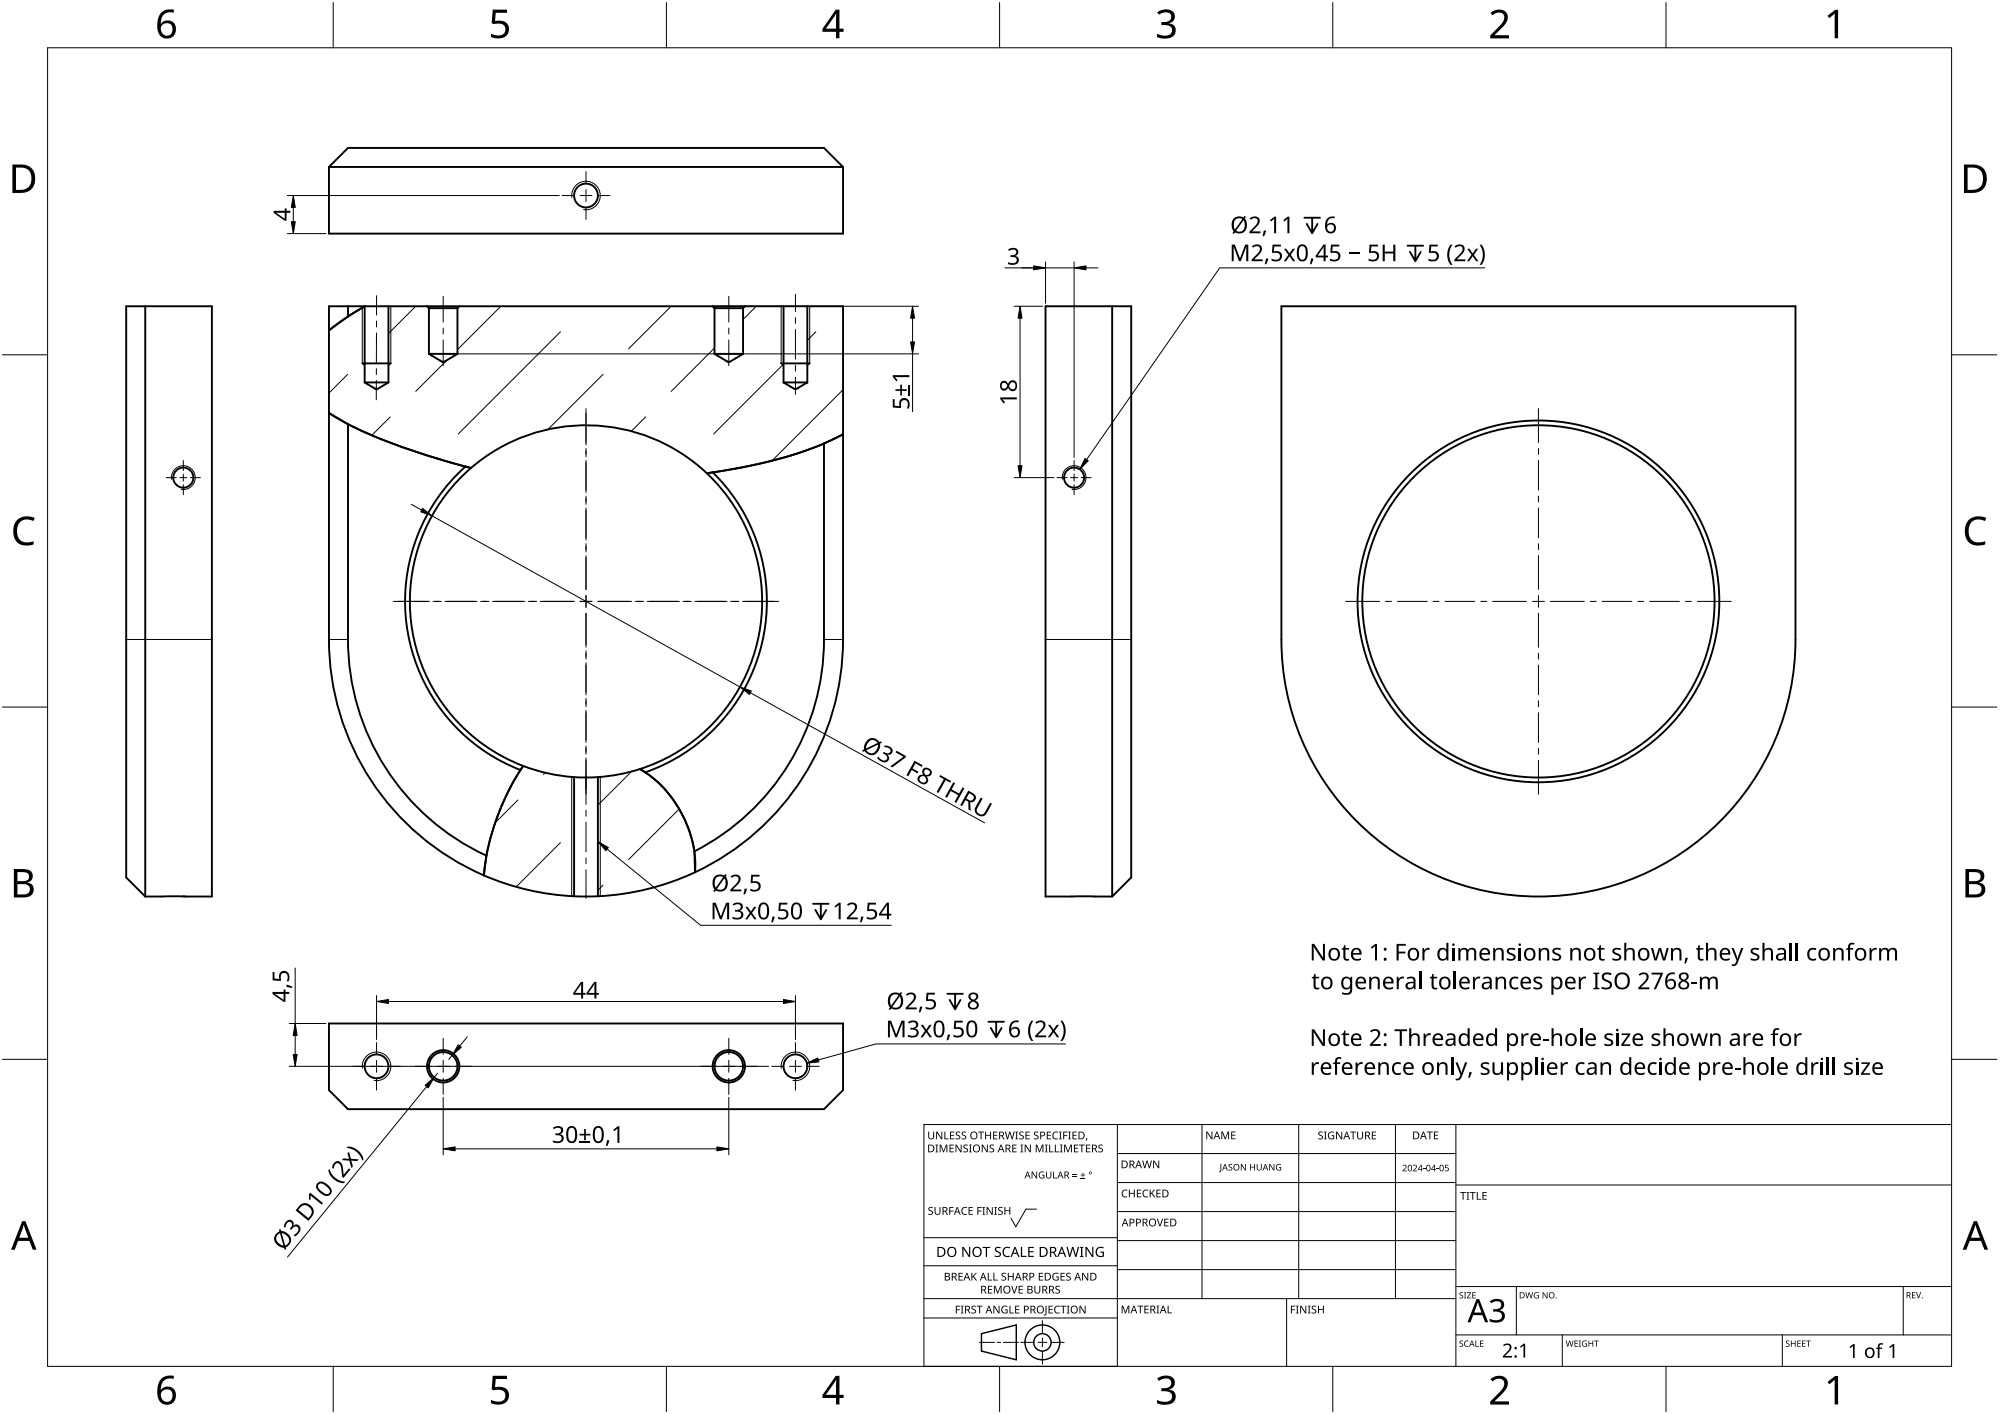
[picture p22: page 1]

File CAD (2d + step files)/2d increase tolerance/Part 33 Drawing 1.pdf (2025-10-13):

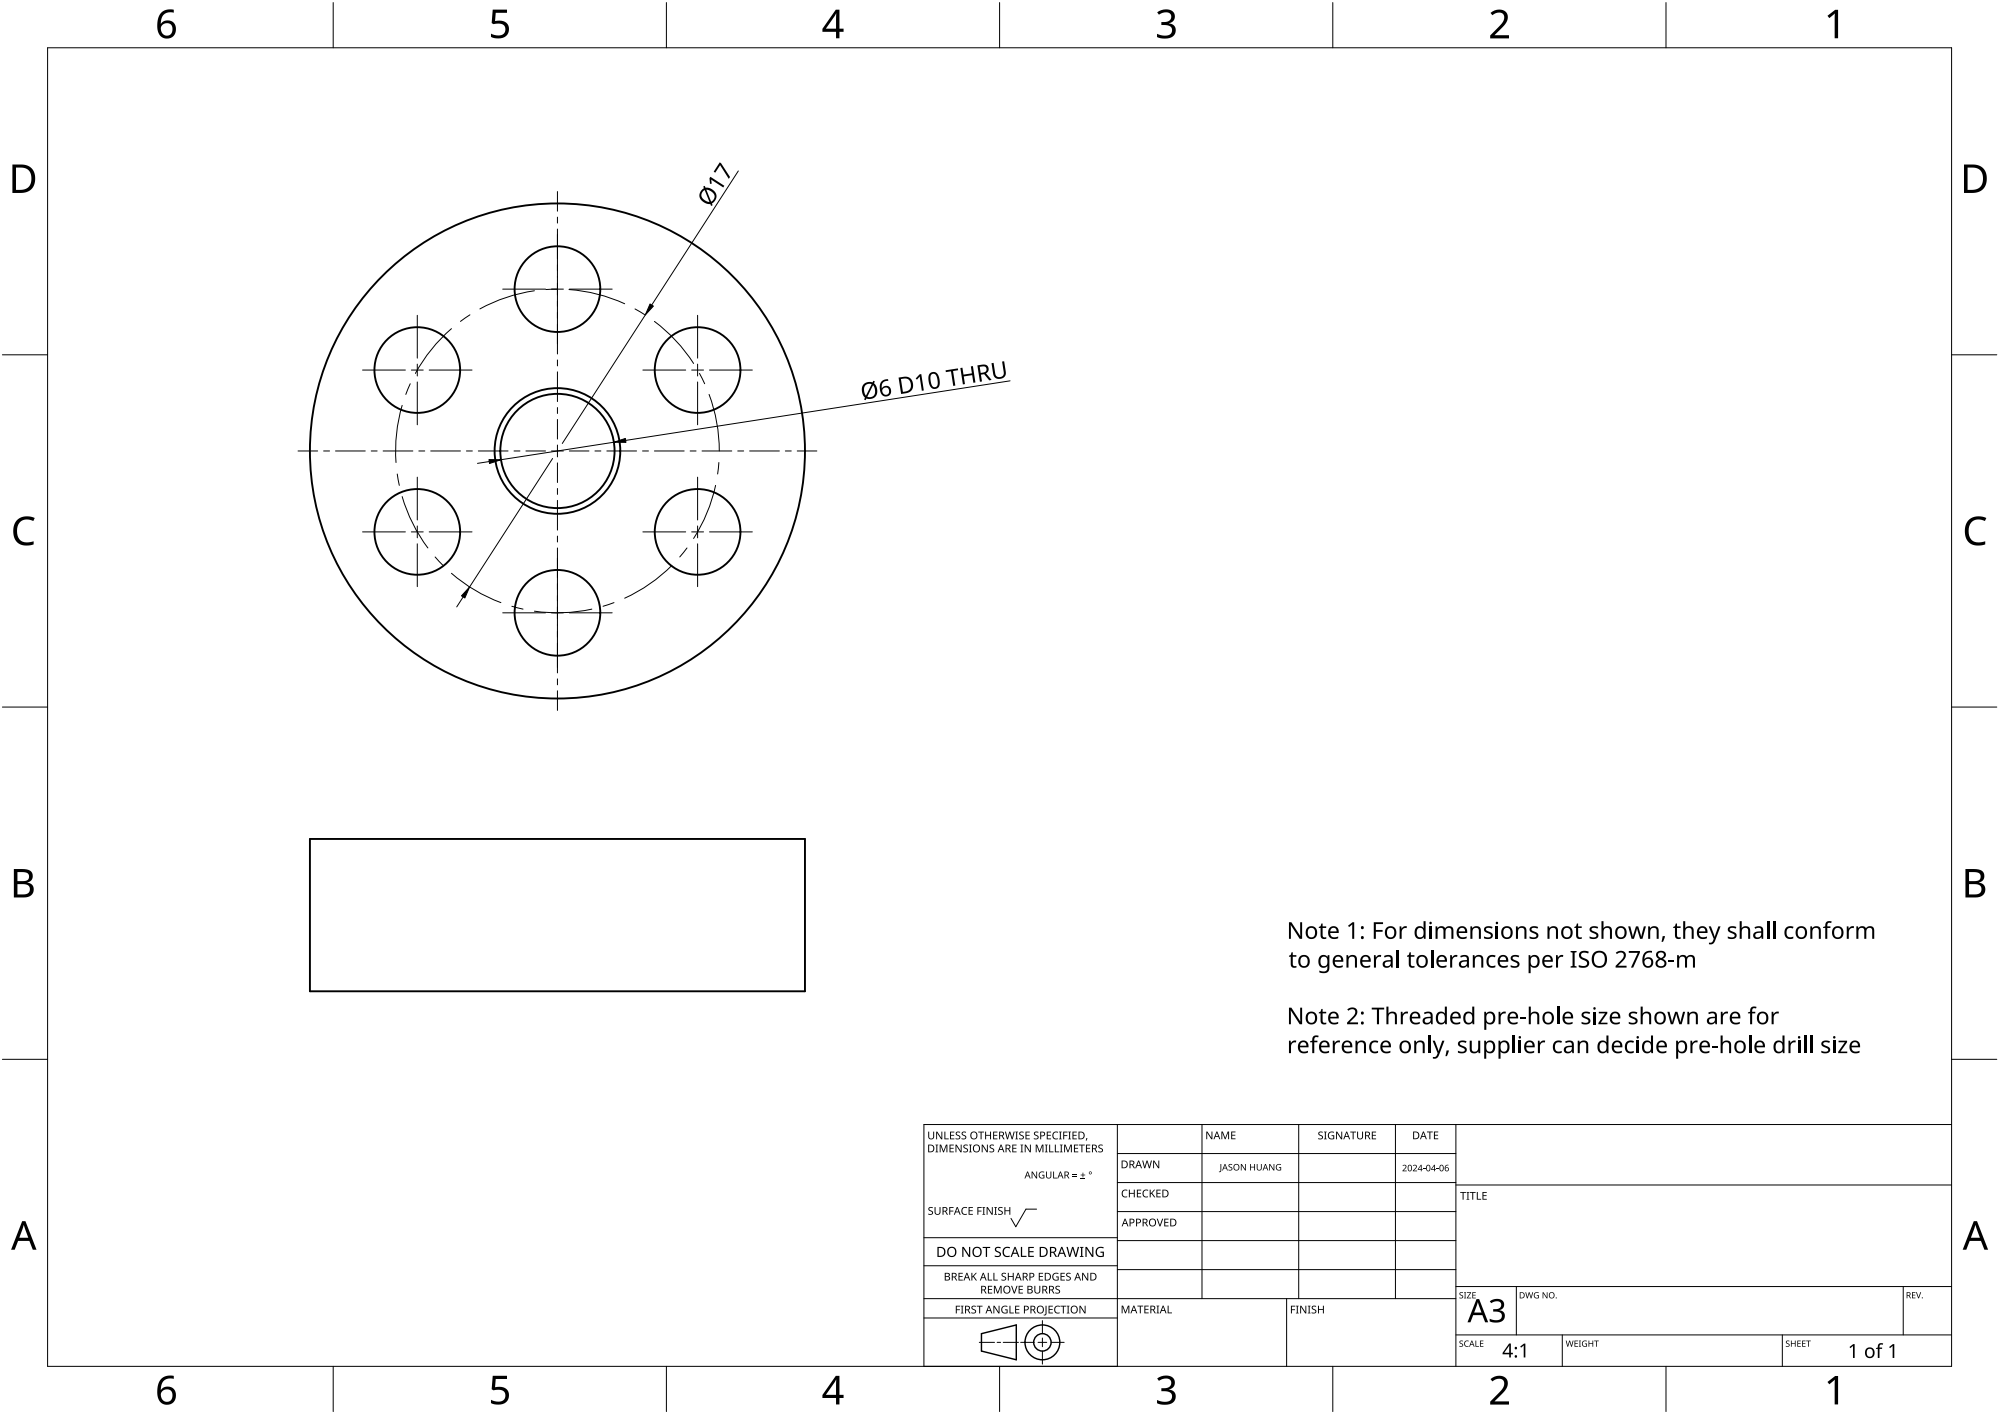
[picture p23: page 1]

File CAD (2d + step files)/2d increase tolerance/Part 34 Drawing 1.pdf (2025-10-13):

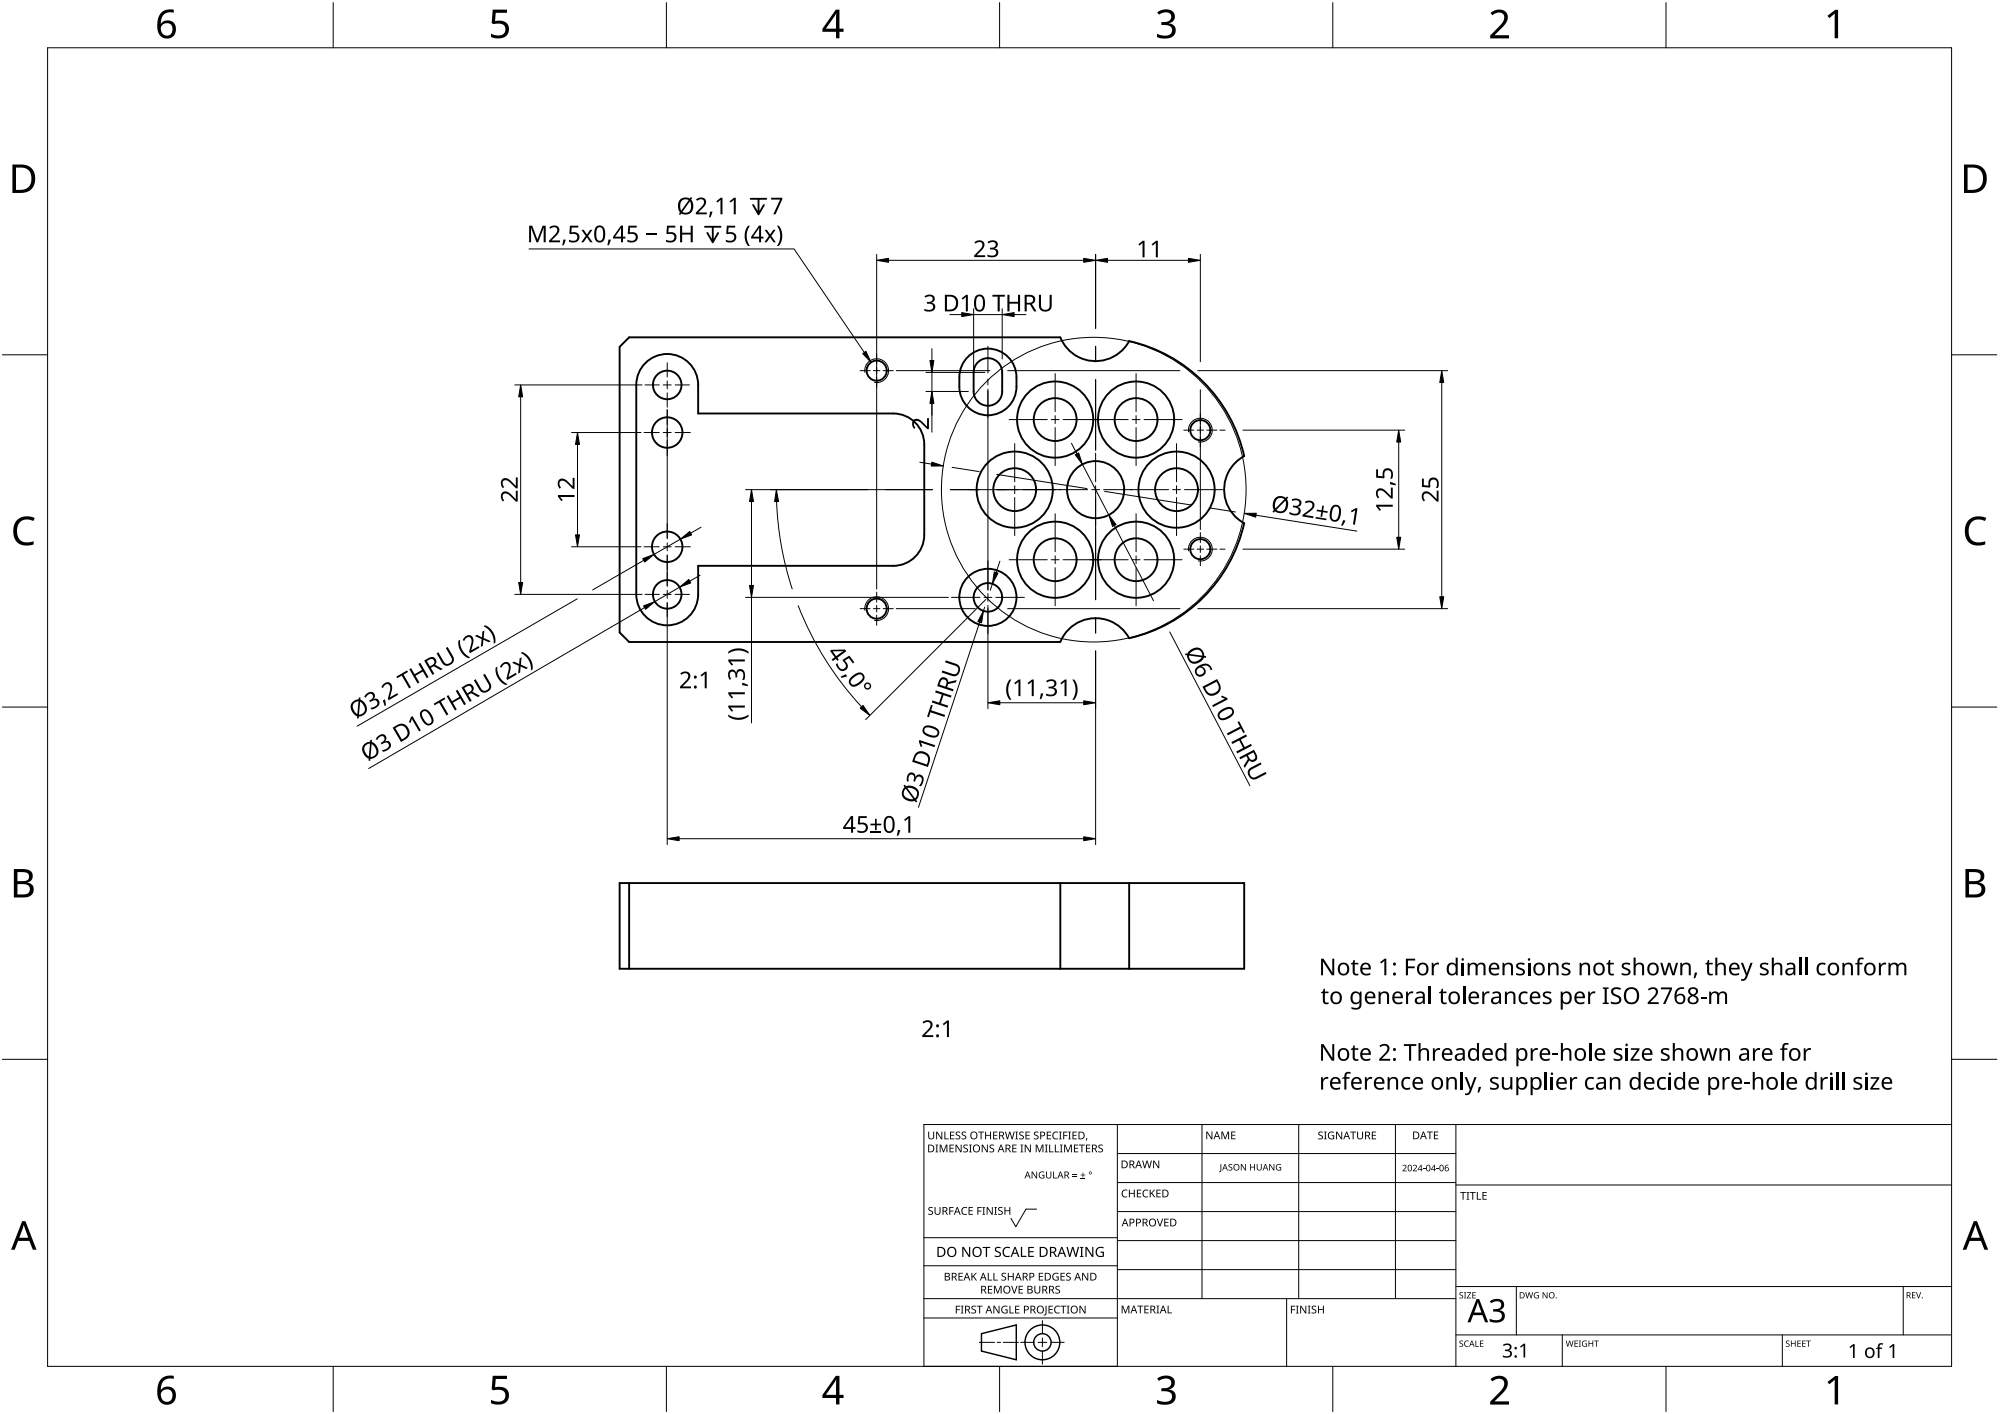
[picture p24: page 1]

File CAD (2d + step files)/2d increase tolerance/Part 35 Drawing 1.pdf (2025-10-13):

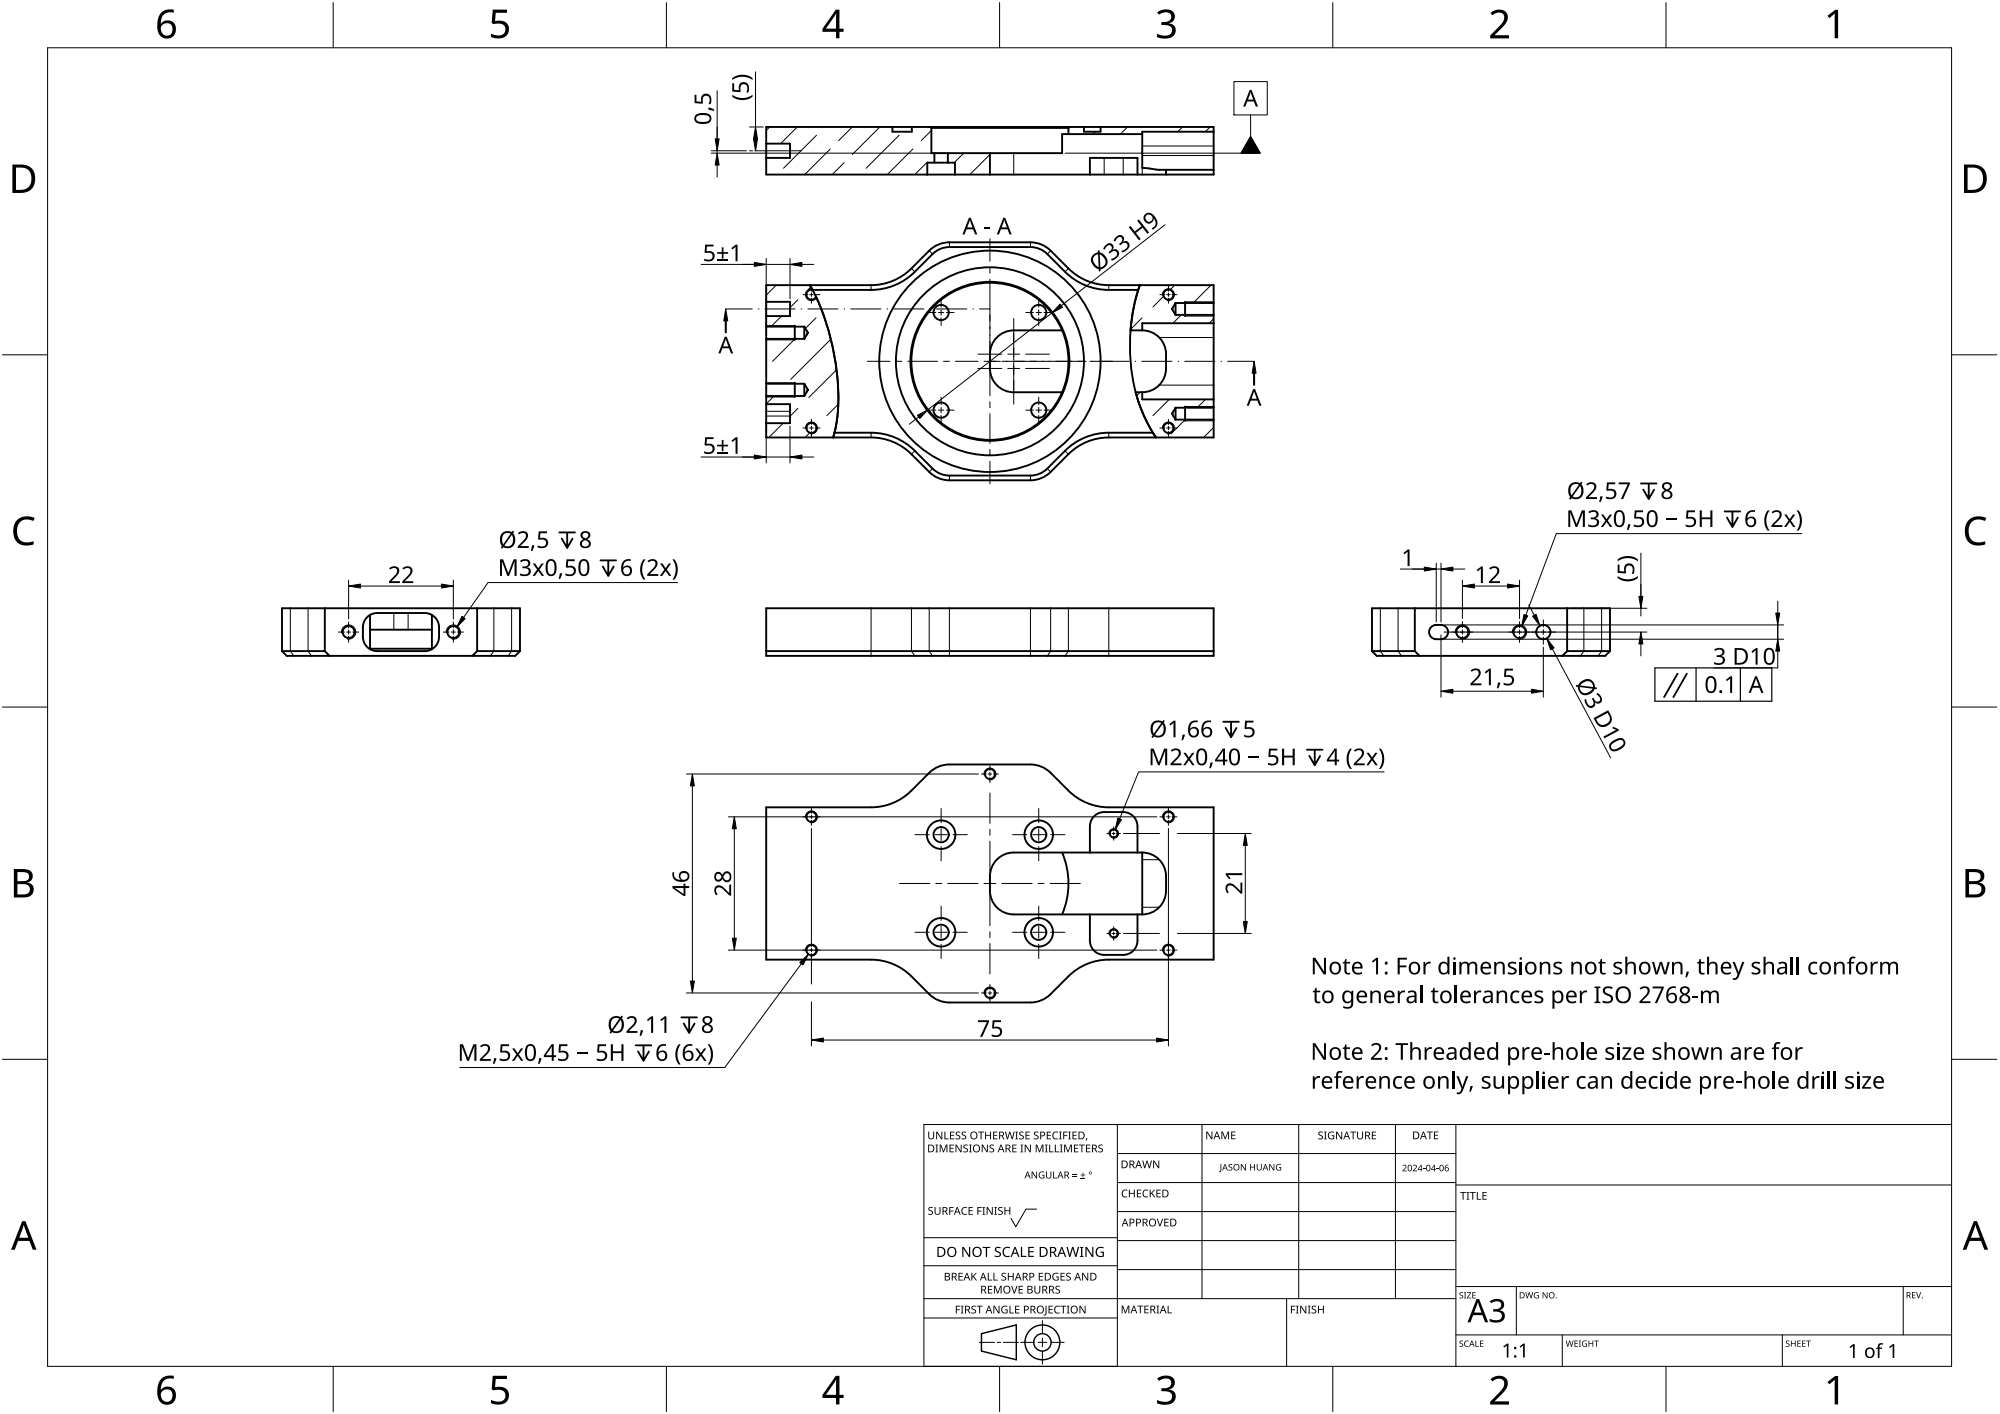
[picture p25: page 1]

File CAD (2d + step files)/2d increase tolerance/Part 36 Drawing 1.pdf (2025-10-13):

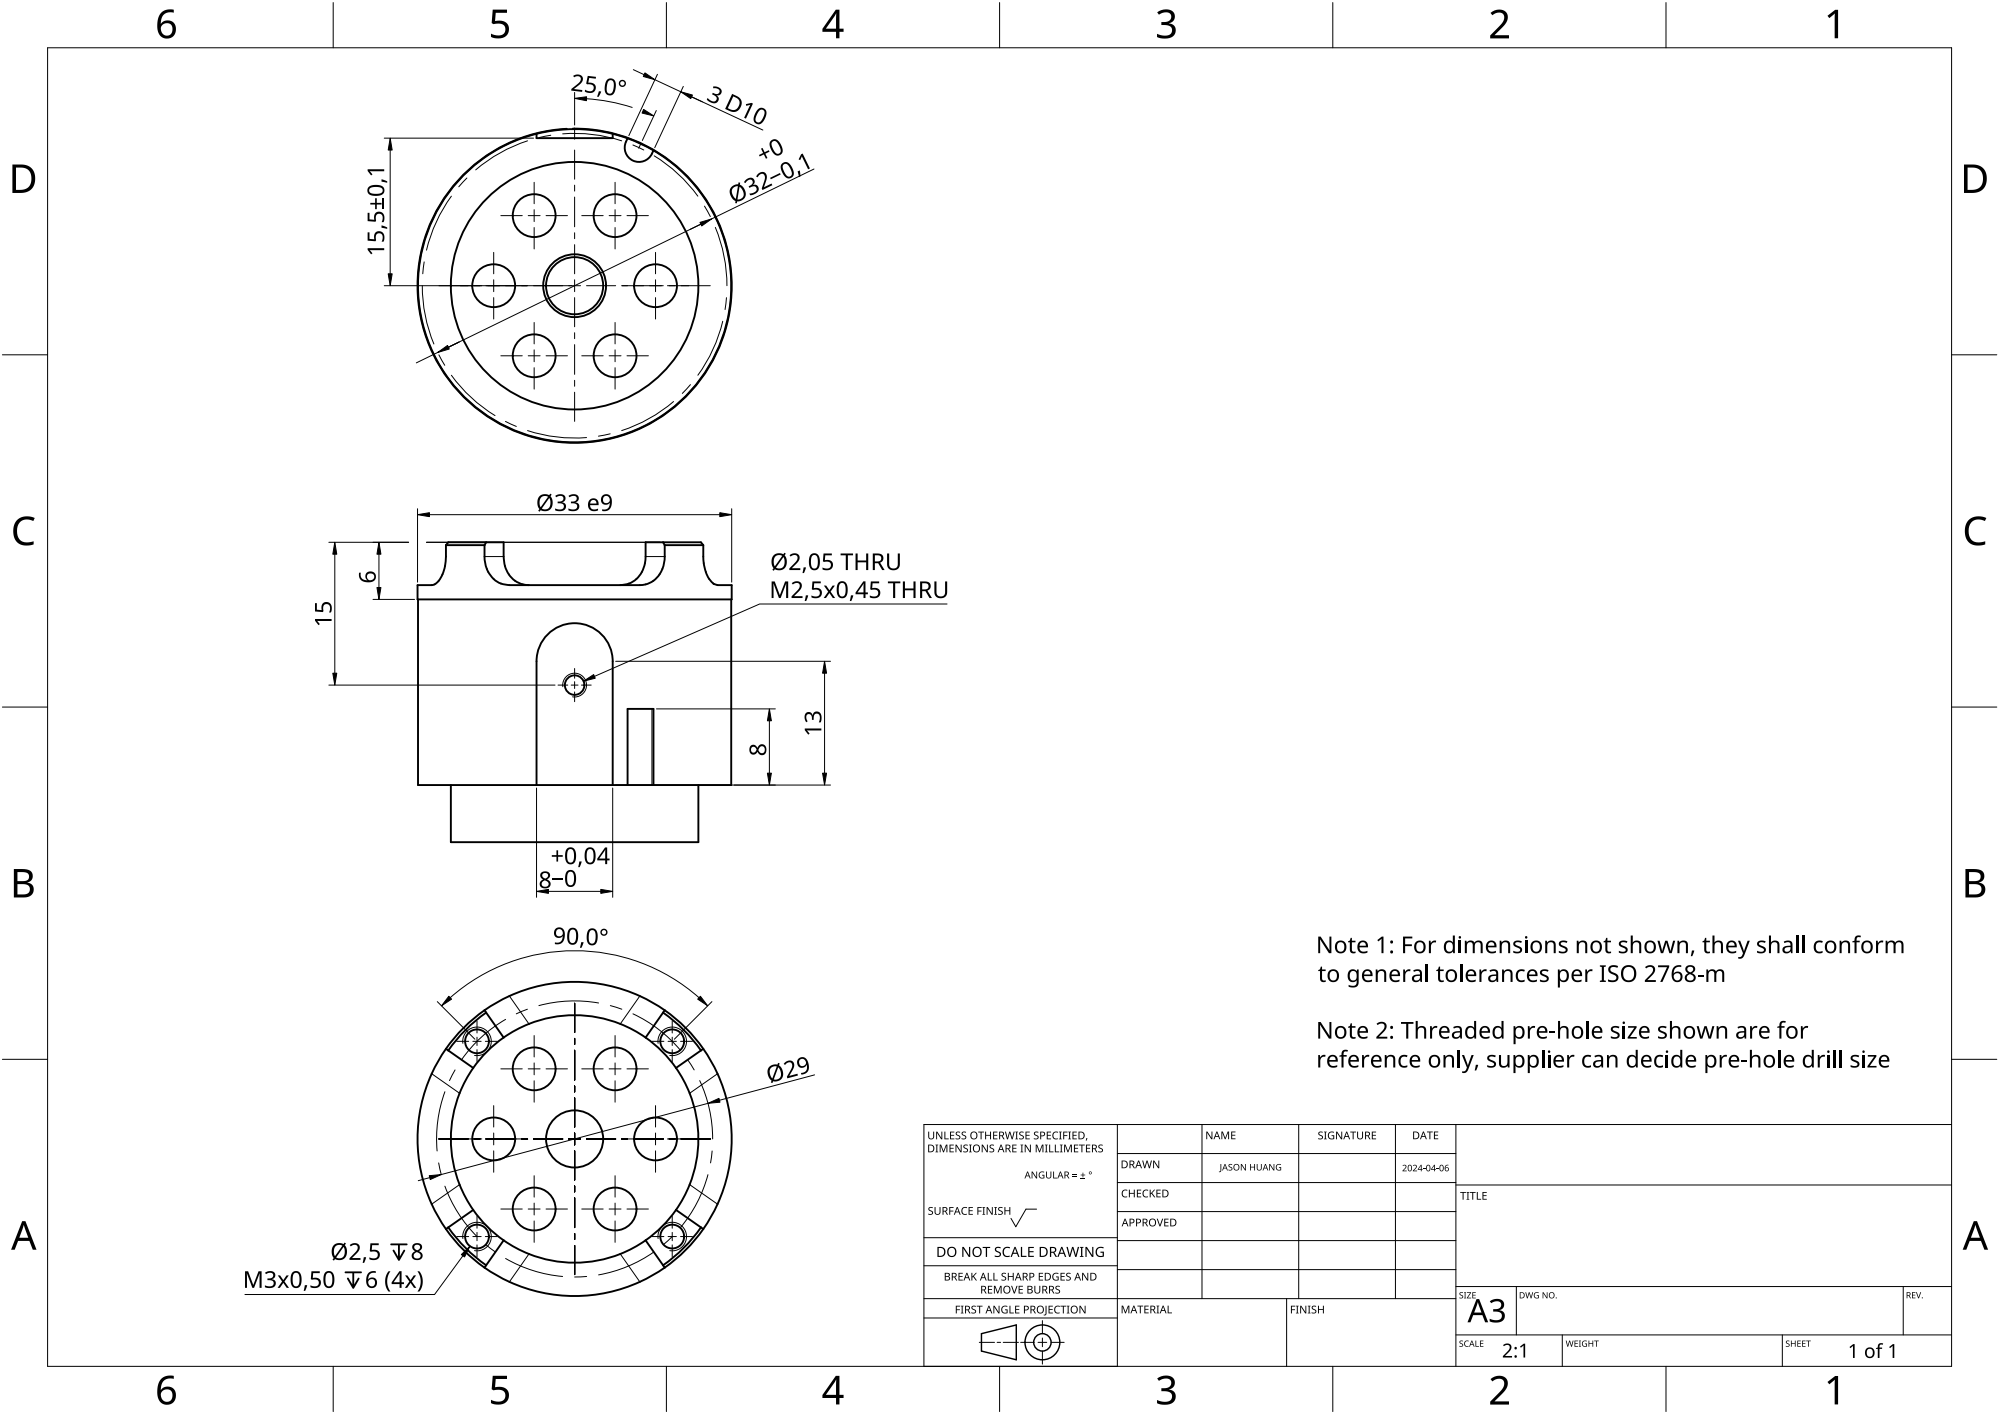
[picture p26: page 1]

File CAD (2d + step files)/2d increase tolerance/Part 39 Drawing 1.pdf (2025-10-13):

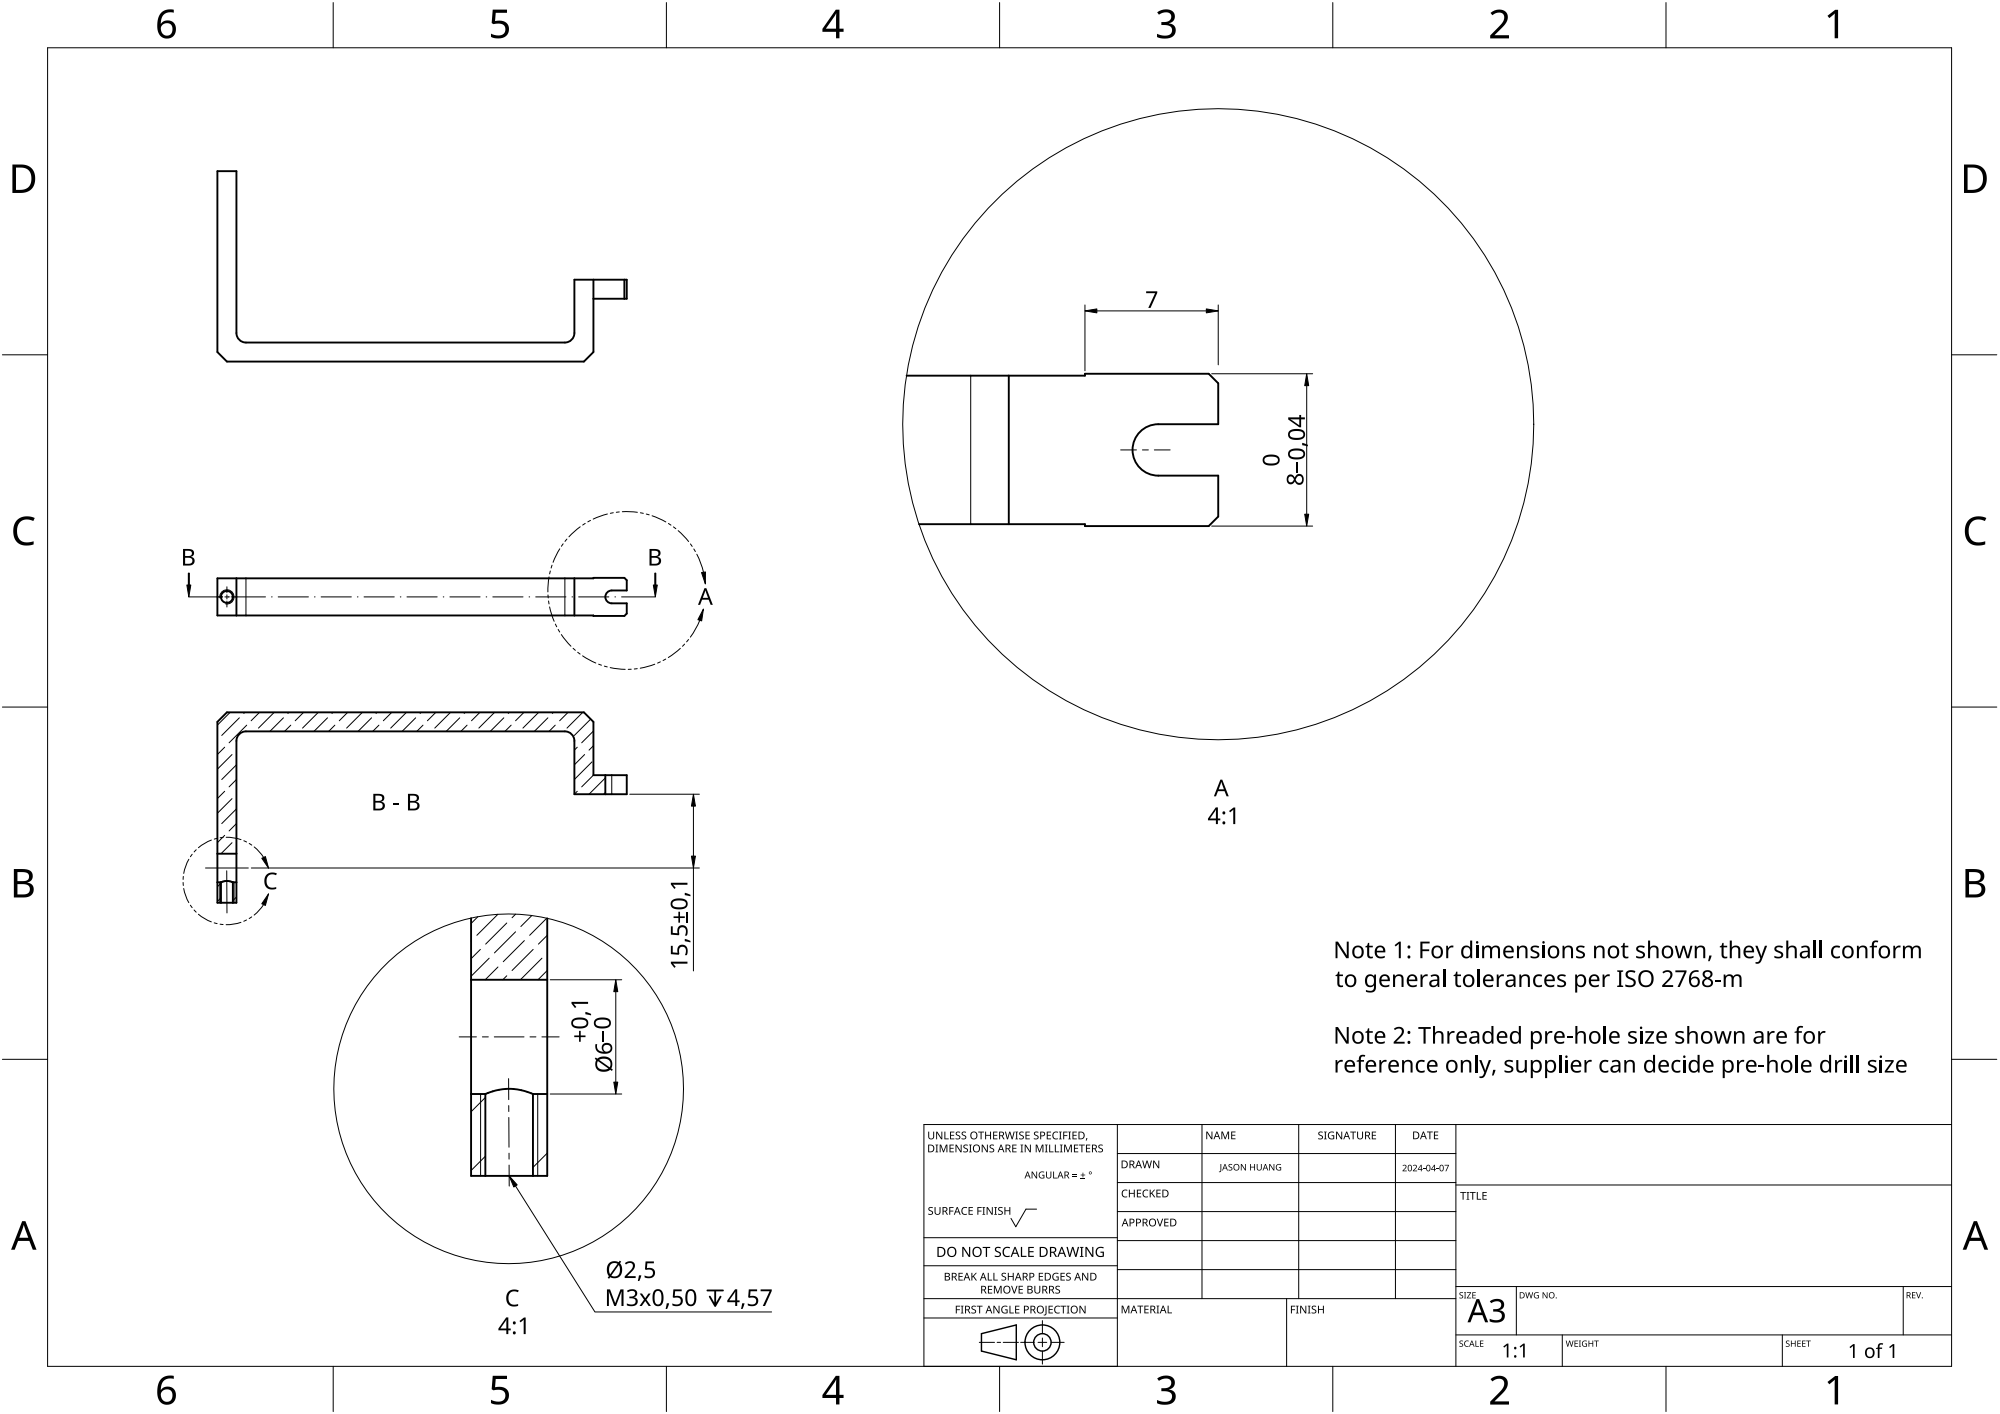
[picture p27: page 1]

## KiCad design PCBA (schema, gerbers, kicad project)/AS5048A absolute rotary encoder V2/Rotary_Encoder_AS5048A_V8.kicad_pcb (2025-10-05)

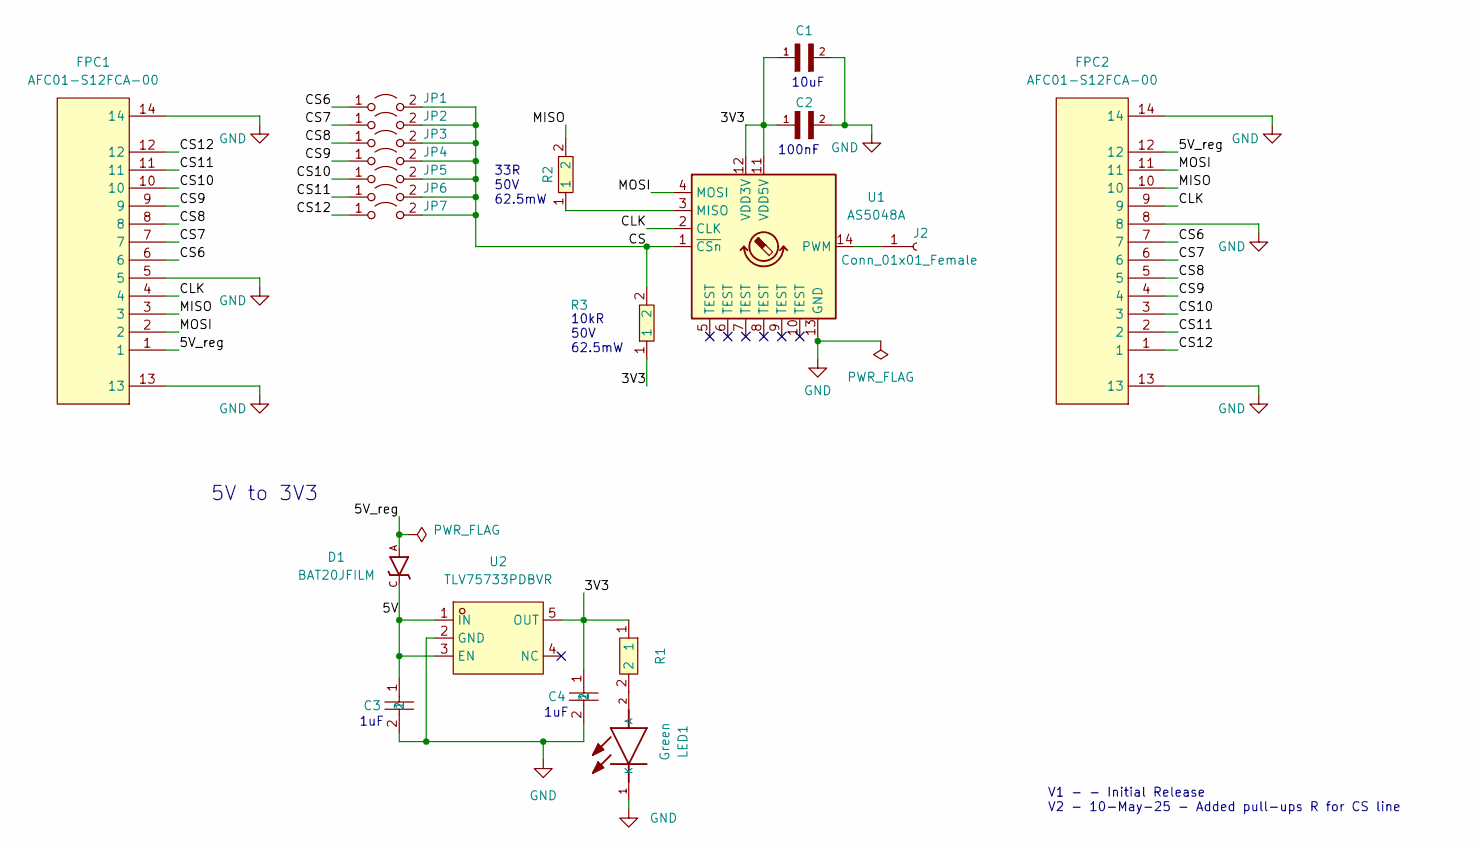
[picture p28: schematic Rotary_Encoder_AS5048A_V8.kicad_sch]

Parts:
C1: GRM155R60J106ME15D; CAPC1005X65N; LCSC C412251
C2: GCM155R71C104KA55J; CAPC1005X55N; LCSC C2655418
C3, C4: CC0603KRX7R7BB105; MLCC_16V_1uF_X7R_±10%_0603_C106248; LCSC Part C106248
D1: BAT20JFILM; SOD-323; LCSC Part # C155590
FPC1, FPC2: AFC01-S12FCA-00; FFC_conn_Flip type_12P_P=0.5mm_C262661; LCSC Part C262661
J2: Conn_01x01_Female; PinHeader_1x01_P1.00mm_Vertical
JP1, JP2, JP3, JP4, JP5, JP6, JP7: Jumper_2_Open; SolderJumper-2_P1.3mm_Open_TrianglePad1.0x1.5mm
LED1: Green; LEDC1608X80N; MOUSER_PART_NUMBER 710-150060GS75000
R1: 0402WGD1001TCE; Resistor_62.5mW_50V_±0.5%_1kΩ_0402_C407754; LCSC Part C407754
R2: RC0402FR-0733RL; Resistor_62.5mW_50V_±1%_33Ω_0402_C138002; LCSC Part C138002
R3: RC0402FR-0710KL; Resistor_62.5mW_50V_±1%_10kΩ_0402_C60490; LCSC Part C60490
U1: AS5048A; TSSOP-14_4.4x5mm_P0.65mm; LCSC C2655181
U2: TLV75733PDBVR; LDO_1A_Fixed_3.3V_out_5.5V_in_SOT-23-5_C485517; LCSC Part C485517

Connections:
/3V3: C1.1, C2.1, C4.1, R1.1, R3.1, U1.11 (VDD5V), U1.12 (VDD3V), U2.5 (OUT)
/5V: C3.1, D1.C, U2.1 (IN), U2.3 (EN)
/5V_reg: D1.A, FPC1.1, FPC2.12
/CLK: FPC1.4, FPC2.9, U1.2 (CLK)
/CS: JP1.2 (B), JP2.2 (B), JP3.2 (B), JP4.2 (B), JP5.2 (B), JP6.2 (B), JP7.2 (B), R3.2, U1.1 (~CSn)
/CS1: FPC1.6, FPC2.7, JP1.1 (A)
/CS2: FPC1.7, FPC2.6, JP2.1 (A)
/CS3: FPC1.8, FPC2.5, JP3.1 (A)
/CS4: FPC1.9, FPC2.4, JP4.1 (A)
/CS5: FPC1.10, FPC2.3, JP5.1 (A)
/CS6: FPC1.11, FPC2.2, JP6.1 (A)
/CS7: FPC1.12, FPC2.1, JP7.1 (A)
/MISO: FPC1.3, FPC2.10, R2.2
/MOSI: FPC1.2, FPC2.11, U1.4 (MOSI)
GND: C1.2, C2.2, C3.2, C4.2, FPC1.5, FPC1.13, FPC1.14, FPC2.8, FPC2.13, FPC2.14, LED1.1 (K), U1.13 (GND), U2.2 (GND)
unnamed: J2.1, U1.14 (PWM)
unnamed: LED1.2 (A), R1.2
unnamed: R2.1, U1.3 (MISO)

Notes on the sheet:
100nF
10kR 50V 62.5mW
1uF
33R 50V 62.5mW
5V to 3V3
10uF
V1 - - Initial Release V2 - 10-May-25 - Added pull-ups R for CS line

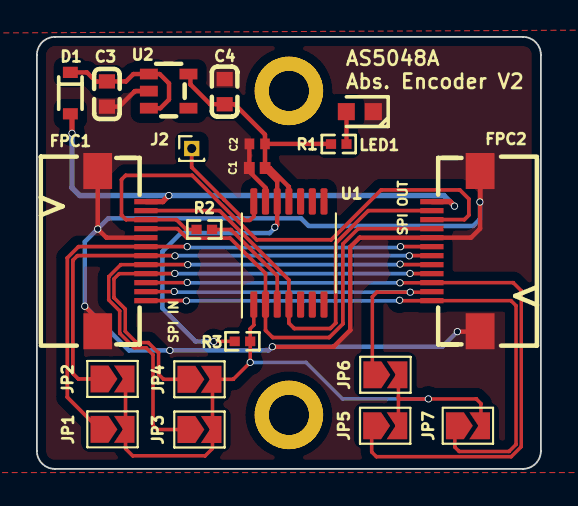
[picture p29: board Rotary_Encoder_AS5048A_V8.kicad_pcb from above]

Board: 2 copper layers, 28.0 x 24.0 mm, 21 parts (0 on the bottom side), 18 nets.

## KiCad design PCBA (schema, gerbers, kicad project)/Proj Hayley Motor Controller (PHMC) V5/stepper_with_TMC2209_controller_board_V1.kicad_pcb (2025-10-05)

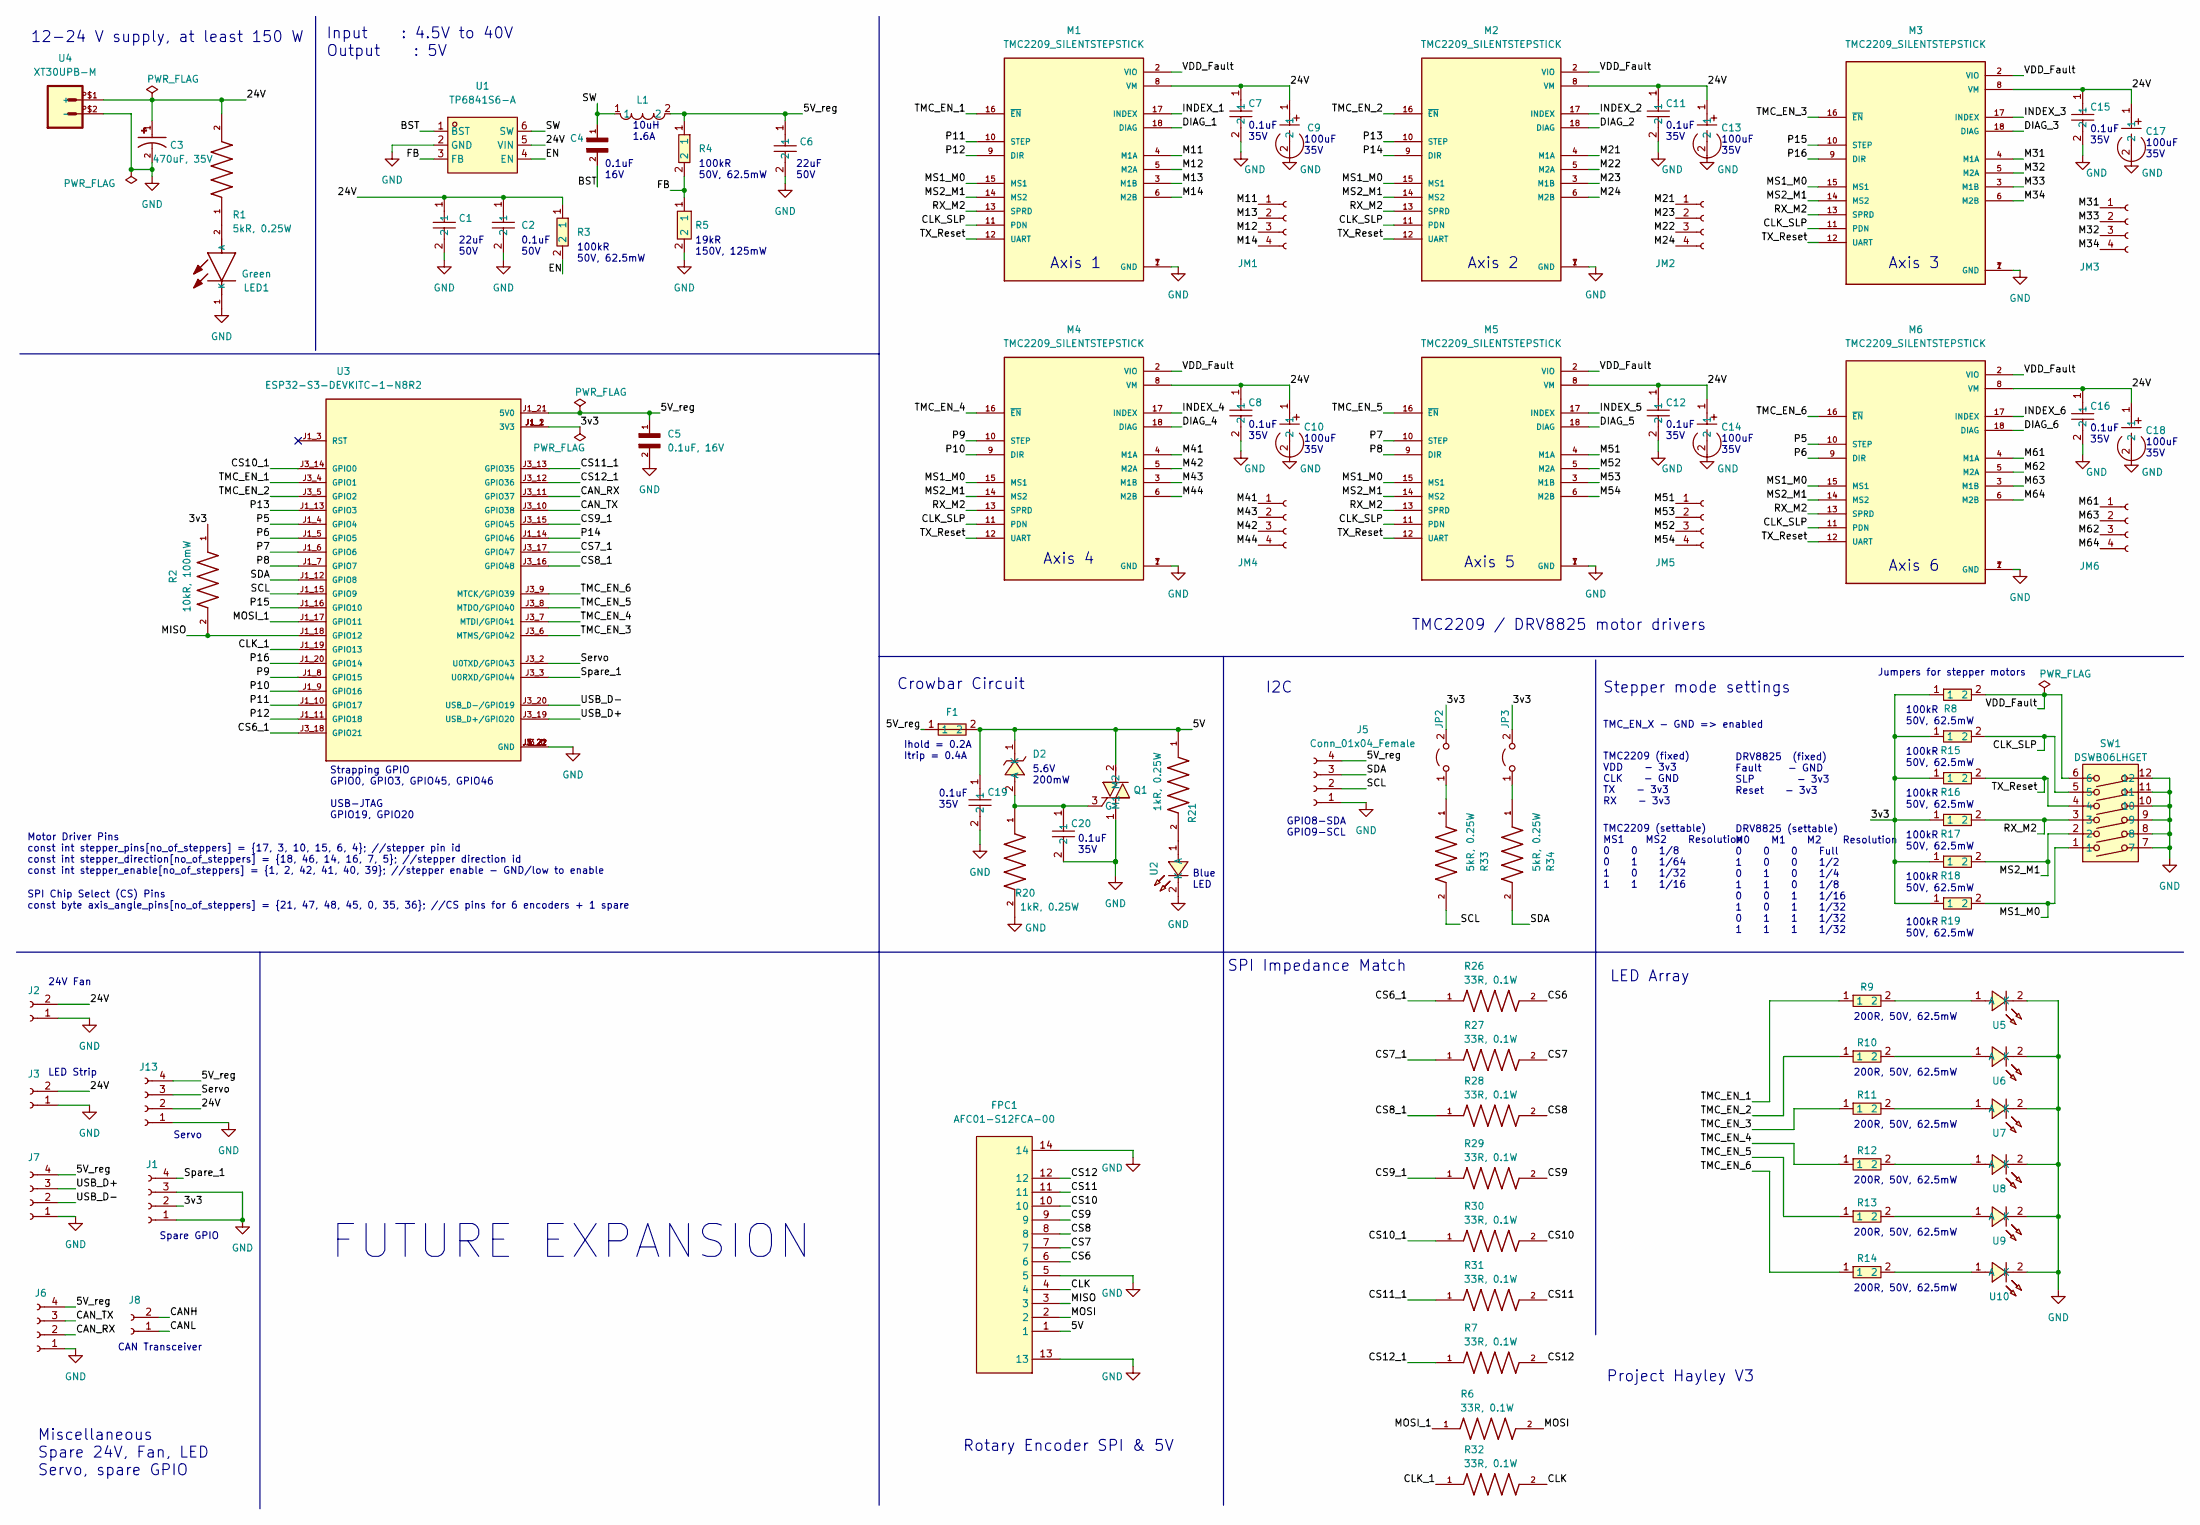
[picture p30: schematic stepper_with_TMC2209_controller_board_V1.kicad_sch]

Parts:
C1, C6: FS55X226K500EHG; Cap_MLCC_50V_22uF_X7R_2220_C784103; LCSC Part C784103
C2: CC0603KRX7R9BB104; MLCC_Yageo_50V_100nF_X7R_±10%_0603_C14663; LCSC Part C14663
C3: 470uF, 35V; CAP_EEHZS1V471P; PARTREV 30-Sep-20; LCSC C403803
C4: GCM155R71C104KA55J; CAPC1005X55N; LCSC Part # C2655418
C5: 0.1uF, 16V; CAPC1005X55N; LCSC C71629
C7, C8, C11, C12, C15, C16, C19, C20: CGA2B3X7R1V104KT0Y0F; C0402_L1.0-W0.5-H0.5; LCSC Part C343047
C9, C10, C13, C14, C17, C18: RVT1V101M0605; Capacitor_100uF_35V_75mA@120Hz_±20%_D6pt3xL5pt4mm_C3151830; LCSC Part C3151830
D2: BZT52C5V6S_C19077441; SOD-323_L1.7-W1.3-LS2.6-RD; LCSC Part C19077441
F1: 0ZCJ0020FF2E; F1206; LCSC Part C6964258
FPC1: AFC01-S12FCA-00; FFC_conn_Flip type_12P_P=0.5mm_C262661; LCSC Part C262661
J1, J5, J7, J13: Conn_01x04_Female; JST_PH_B4B-PH-K_1x04_P2.00mm_Vertical
J2, J3, J8: Conn_01x02_Female; JST_EH_B2B-EH-A_1x02_P2.50mm_Vertical
J6: Conn_01x04_Female; JST_EH_B4B-EH-A_1x04_P2.50mm_Vertical
JM1, JM2, JM3, JM4, JM5, JM6: Conn_01x04_Female; JST_XH_B4B-XH-A_1x04_P2.50mm_Vertical
JP2, JP3: Jumper_2_Open; SolderJumper-2_P1.3mm_Open_TrianglePad1.0x1.5mm
L1: FTC252012S100MBCA; Inductor_10uH_1pt6A_2x2pt5mm_C5832376; LCSC Part C5832376
LED1: Green; LEDC1608X80N; MOUSER_PART_NUMBER 710-150060GS75000
M1, M2, M3, M4, M5, M6: TMC2209_SILENTSTEPSTICK; MODULE_TMC2209_SILENTSTEPSTICK; PARTREV 1.20
Q1: MAC97A8-23-3L; SOT-23-3_L2.9-W1.6-P1.90-LS2.8-BL-A; LCSC Part C2831929
R1, R33, R34: 5kR, 0.25W; RESC3116X65N; LCSC Part # C870818
R2: 10kR, 100mW; RESC1607X60N; LCSC Part # C98220
R3, R4, R8, R15, R16, R17, R18, R19: RC0402FR-07100KL; Resistor_ 100kΩ_62.5mW_50V_0402_C60491; LCSC Part C60491
R5: FRC0805F1902TS; Resistor_19kΩ_0.125W_150V_0805_C2930177; LCSC Part C2930177
R6, R7, R26, R27, R28, R29, R30, R31, R32: 33R, 0.1W; RESC1608X55N; LCSC Part # C108407
R9, R10, R11, R12, R13, R14: 0402WGF2000TCE; R0402; LCSC Part C25087
R20, R21: 1kR, 0.25W; RESC3116X65N; LCSC Part # C131398
SW1: DSWB06LHGET; 6_SPST_Through_Hole_DIP_C99416; LCSC Part C99416
U1: TP6841S6-A; SOT-23-6_L2.9-W1.6-P0.95-LS2.8-BL; LCSC Part C2844924
U2, U5, U6, U7, U8, U9, U10: XL-1608UBC-06A; Blue_LED_5mA_456nm~476nm_130°_2.6V~3V_0603_C7371904; LCSC Part C7371904
U3: ESP32-S3-DEVKITC-1-N8R2; XCVR_ESP32-S3-DEVKITC-1-N8R2; PARTREV V1
U4: XT30UPB-M; LCSC Part # C108769

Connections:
/3v3: J1.2, JP2.2 (B), JP3.2 (B), R2.1, R8.1, R15.1, R16.1, R17.1, R18.1, R19.1, U3.J1_1 (3V3), U3.J1_2 (3V3)
/5V: C19.1, D2.1 (K), F1.2, FPC1.1, Q1.2 (M2), R21.1
/5V_reg: C5.1, C6.1, F1.1, J5.4, J6.4, J7.4, J13.4, L1.2, R4.1, U3.J1_21 (5V0)
/24V: C1.1, C2.1, C3.1, C7.1, C8.1, C9.1, C10.1, C11.1, C12.1, C13.1, C14.1, C15.1, C16.1, C17.1, C18.1, J2.2, J3.2, J13.2, M1.8 (VM), M2.8 (VM), M3.8 (VM), M4.8 (VM), M5.8 (VM), M6.8 (VM), R1.2, R3.1, U1.5 (VIN), U4.P$1 (+)
/BST: C4.2, U1.1 (BST)
/CANH: J8.2
/CANL: J8.1
/CAN_RX: J6.2, U3.J3_11 (GPIO37)
/CAN_TX: J6.3, U3.J3_10 (GPIO38)
/CLK: FPC1.4, R32.2
/CLK_1: R32.1, U3.J1_19 (GPIO13)
/CLK_SLP: M1.11 (PDN), M2.11 (PDN), M3.11 (PDN), M4.11 (PDN), M5.11 (PDN), M6.11 (PDN), R15.2, SW1.5
/CS6: FPC1.6, R26.2
/CS6_1: R26.1, U3.J3_18 (GPIO21)
/CS7: FPC1.7, R27.2
/CS7_1: R27.1, U3.J3_17 (GPIO47)
/CS8: FPC1.8, R28.2
/CS8_1: R28.1, U3.J3_16 (GPIO48)
/CS9: FPC1.9, R29.2
/CS9_1: R29.1, U3.J3_15 (GPIO45)
/CS10: FPC1.10, R30.2
/CS10_1: R30.1, U3.J3_14 (GPIO0)
/CS11: FPC1.11, R31.2
/CS11_1: R31.1, U3.J3_13 (GPIO35)
/CS12: FPC1.12, R7.2
/CS12_1: R7.1, U3.J3_12 (GPIO36)
/DIAG_1: M1.18 (DIAG)
/DIAG_2: M2.18 (DIAG)
/DIAG_3: M3.18 (DIAG)
/DIAG_4: M4.18 (DIAG)
/DIAG_5: M5.18 (DIAG)
/DIAG_6: M6.18 (DIAG)
/EN: R3.2, U1.4 (EN)
/FB: R4.2, R5.1, U1.3 (FB)
/INDEX_1: M1.17 (INDEX)
/INDEX_2: M2.17 (INDEX)
/INDEX_3: M3.17 (INDEX)
/INDEX_4: M4.17 (INDEX)
/INDEX_5: M5.17 (INDEX)
/INDEX_6: M6.17 (INDEX)
/M11: JM1.1, M1.4 (M1A)
/M12: JM1.3, M1.5 (M2A)
/M13: JM1.2, M1.3 (M1B)
/M14: JM1.4, M1.6 (M2B)
/M21: JM2.1, M2.4 (M1A)
/M22: JM2.3, M2.5 (M2A)
/M23: JM2.2, M2.3 (M1B)
/M24: JM2.4, M2.6 (M2B)
/M31: JM3.1, M3.4 (M1A)
/M32: JM3.3, M3.5 (M2A)
/M33: JM3.2, M3.3 (M1B)
/M34: JM3.4, M3.6 (M2B)
/M41: JM4.1, M4.4 (M1A)
/M42: JM4.3, M4.5 (M2A)
/M43: JM4.2, M4.3 (M1B)
/M44: JM4.4, M4.6 (M2B)
/M51: JM5.1, M5.4 (M1A)
/M52: JM5.3, M5.5 (M2A)
/M53: JM5.2, M5.3 (M1B)
/M54: JM5.4, M5.6 (M2B)
/M61: JM6.1, M6.4 (M1A)
/M62: JM6.3, M6.5 (M2A)
/M63: JM6.2, M6.3 (M1B)
/M64: JM6.4, M6.6 (M2B)
/MISO: FPC1.3, R2.2, U3.J1_18 (GPIO12)
/MOSI: FPC1.2, R6.2
/MOSI_1: R6.1, U3.J1_17 (GPIO11)
/MS1_M0: M1.15 (MS1), M2.15 (MS1), M3.15 (MS1), M4.15 (MS1), M5.15 (MS1), M6.15 (MS1), R19.2, SW1.1
/MS2_M1: M1.14 (MS2), M2.14 (MS2), M3.14 (MS2), M4.14 (MS2), M5.14 (MS2), M6.14 (MS2), R18.2, SW1.2
/P5: M6.10 (STEP), U3.J1_4 (GPIO4)
/P6: M6.9 (DIR), U3.J1_5 (GPIO5)
/P7: M5.10 (STEP), U3.J1_6 (GPIO6)
/P8: M5.9 (DIR), U3.J1_7 (GPIO7)
/P9: M4.10 (STEP), U3.J1_8 (GPIO15)
/P10: M4.9 (DIR), U3.J1_9 (GPIO16)
/P11: M1.10 (STEP), U3.J1_10 (GPIO17)
/P12: M1.9 (DIR), U3.J1_11 (GPIO18)
/P13: M2.10 (STEP), U3.J1_13 (GPIO3)
/P14: M2.9 (DIR), U3.J1_14 (GPIO46)
/P15: M3.10 (STEP), U3.J1_16 (GPIO10)
/P16: M3.9 (DIR), U3.J1_20 (GPIO14)
/RX_M2: M1.13 (SPRD), M2.13 (SPRD), M3.13 (SPRD), M4.13 (SPRD), M5.13 (SPRD), M6.13 (SPRD), R17.2, SW1.3
/SCL: J5.2, R33.2, U3.J1_15 (GPIO9)
/SDA: J5.3, R34.2, U3.J1_12 (GPIO8)
/SW: C4.1, L1.1, U1.6 (SW)
/Servo: J13.3, U3.J3_2 (U0TXD/GPIO43)
/Spare_1: J1.4, U3.J3_3 (U0RXD/GPIO44)
/TMC_EN_1: M1.16 (~EN), R9.1, U3.J3_4 (GPIO1)
/TMC_EN_2: M2.16 (~EN), R10.1, U3.J3_5 (GPIO2)
/TMC_EN_3: M3.16 (~EN), R11.1, U3.J3_6 (MTMS/GPIO42)
/TMC_EN_4: M4.16 (~EN), R12.1, U3.J3_7 (MTDI/GPIO41)
/TMC_EN_5: M5.16 (~EN), R13.1, U3.J3_8 (MTDO/GPIO40)
/TMC_EN_6: M6.16 (~EN), R14.1, U3.J3_9 (MTCK/GPIO39)
/TX_Reset: M1.12 (UART), M2.12 (UART), M3.12 (UART), M4.12 (UART), M5.12 (UART), M6.12 (UART), R16.2, SW1.4
/USB_D+: J7.3, U3.J3_19 (USB_D+/GPIO20)
/USB_D-: J7.2, U3.J3_20 (USB_D-/GPIO19)
/VDD_Fault: M1.2 (VIO), M2.2 (VIO), M3.2 (VIO), M4.2 (VIO), M5.2 (VIO), M6.2 (VIO), R8.2, SW1.6
GND: C1.2, C2.2, C3.2, C5.2, C6.2, C7.2, C8.2, C9.2, C10.2, C11.2, C12.2, C13.2, C14.2, C15.2, C16.2, C17.2, C18.2, C19.2, C20.2, FPC1.5, FPC1.13, FPC1.14, J1.1, J1.3, J2.1, J3.1, J5.1, J6.1, J7.1, J13.1, LED1.1 (K), M1.1 (GND), M1.7 (GND), M2.1 (GND), M2.7 (GND), M3.1 (GND), M3.7 (GND), M4.1 (GND), M4.7 (GND), M5.1 (GND), M5.7 (GND), M6.1 (GND), M6.7 (GND), Q1.1 (M1), R5.2, R20.2, SW1.7, SW1.8, SW1.9, SW1.10, SW1.11, SW1.12, U1.2 (GND), U2.2 (K), U3.J1_22 (GND), U3.J3_1 (GND), U3.J3_21 (GND), U3.J3_22 (GND), U4.P$2 (-), U5.2 (K), U6.2 (K), U7.2 (K), U8.2 (K), U9.2 (K), U10.2 (K)
unnamed: C20.1, D2.2 (A), Q1.3 (G), R20.1
unnamed: JP2.1 (A), R33.1
unnamed: JP3.1 (A), R34.1
unnamed: LED1.2 (A), R1.1
unnamed: R9.2, U5.1 (A)
unnamed: R10.2, U6.1 (A)
unnamed: R11.2, U7.1 (A)
unnamed: R12.2, U8.1 (A)
unnamed: R13.2, U9.1 (A)
unnamed: R14.2, U10.1 (A)
unnamed: R21.2, U2.1 (A)

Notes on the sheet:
100uF 35V
Jumpers for stepper motors
TMC2209 (fixed) VDD - 3v3 CLK - GND TX - 3v3 RX - 3v3
Project Hayley V3
100kR 50V, 62.5mW
Miscellaneous Spare 24V, Fan, LED Servo, spare GPIO
0.1uF 35V
200R, 50V, 62.5mW
22uF 50V
DRV8825 (settable) M0 M1 M2 Resolution 0 0 0 Full 1 0 0 1/2 0 1 0 1/4 1 1 0 1/8 0 0 1 1/16 1 0 1 1/32 0 1 1 1/32 1 1 1 1/32
Crowbar Circuit
Spare GPIO
Axis 2
Rotary Encoder SPI & 5V
0.1uF 50V
10uH 1.6A
0.1uF 16V
Axis 1
GPIO8-SDA GPIO9-SCL
19kR 150V, 125mW
TMC2209 (settable) MS1 MS2 Resolution 0 0 1/8 0 1 1/64 1 0 1/32 1 1 1/16
Strapping GPIO GPIO0, GPIO3, GPIO45, GPIO46 USB-JTAG GPIO19, GPIO20
LED Array
SPI Chip Select (CS) Pins const byte axis_angle_pins[no_of_steppers] = {21, 47, 48, 45, 0, 35, 36}; //CS pins for 6 encoders + 1 spare
Servo
DRV8825 (fixed) Fault - GND SLP - 3v3 Reset - 3v3
Stepper mode settings
TMC_EN_X - GND => enabled
Axis 6
5.6V 200mW
LED Strip
SPI Impedance Match
I2C
Input : 4.5V to 40V Output : 5V
Axis 3
24V Fan
Ihold = 0.2A Itrip = 0.4A
Axis 4
Blue LED
FUTURE EXPANSION

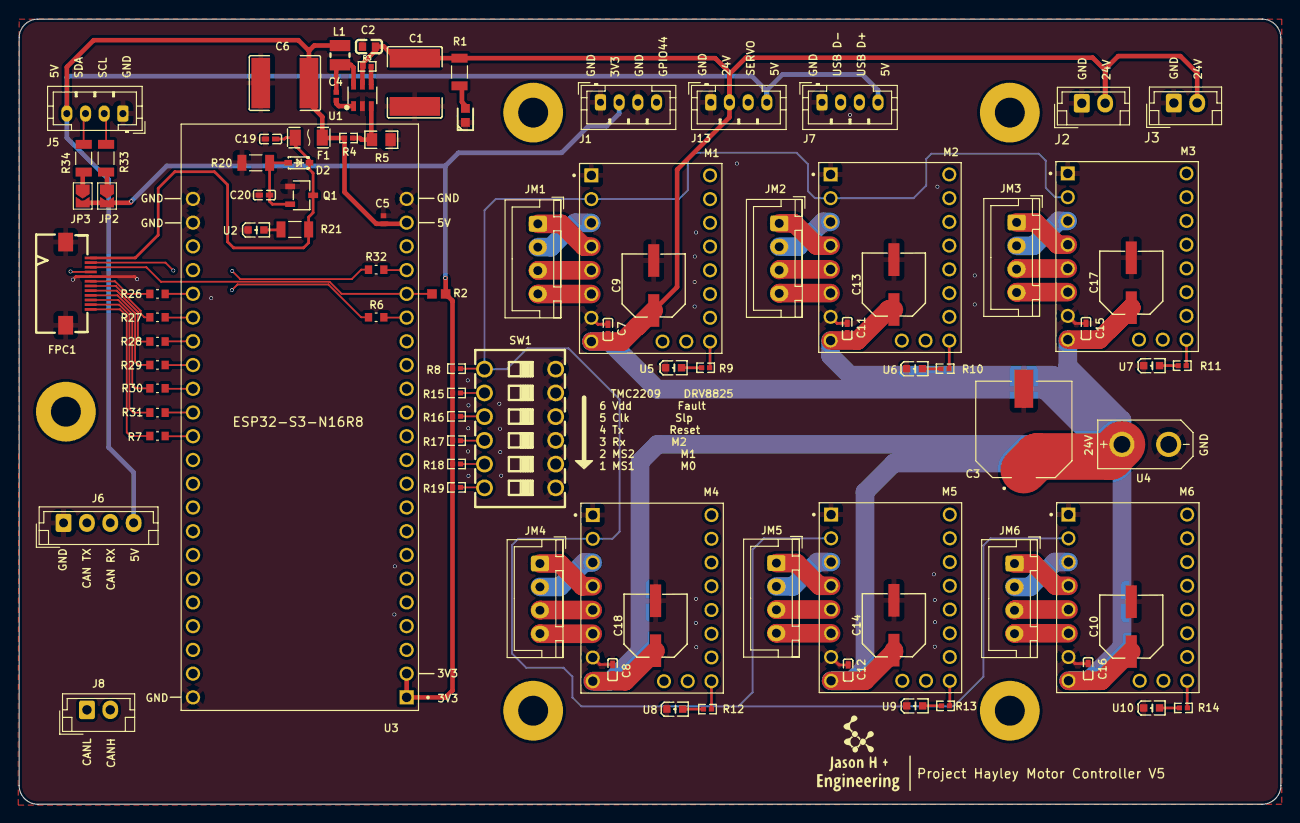
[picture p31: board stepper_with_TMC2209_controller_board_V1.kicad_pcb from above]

Board: 4 copper layers, 135.0 x 84.0 mm, 89 parts (0 on the bottom side), 95 nets.

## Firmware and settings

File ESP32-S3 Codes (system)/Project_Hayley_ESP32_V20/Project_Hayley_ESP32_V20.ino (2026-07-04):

/*

V4  - Cleanup and add homing capability, verified working with "Project_Hayley_V4_IK_user_interface_V04.py"
V5  - Corrected encoder pins sequence for Axis 1-6, compatible with "Project_Hayley_V4_IK_user_interface_V06.py"
V6  - attempt to concise the code (using a struct for stepper_position_data), compatible with "Project_Hayley_V4_IK_user_interface_V07.py"
V7  - Successfully added FreeRTOS queue. Compatible with "Project_Hayley_V4_IK_user_interface_V07.py"
V8  - Removal of homing and recalibration logic here as the user interface side (Python) will be zeroing to home base on encoder "home" readings
    - Compatible with "Project_Hayley_V4_IK_user_interface_V08.py" 
V9  - major change attempt to switch steps calculation from python/raspberry side to ESP32
    - The zero angles/position data need to be hardcoded on ESP32 instead
    - motor steps calculation parked under run_stepper() 
    - python/raspberry side need to send in desired relative angular positions instead of sending the relative steps
    - updated to send encoder as float instead of as long
V10 - Cleanup
    - as a consequence of V9, recalibrate & homing functions are now removed
    - combined some struct declarations for efficiency. e.g. struct with relative_target, encoder; struct with motor, distance_to_go
    - add encoder-stepper close loop, Compatible with "Project_Hayley_V4_IK_user_interface_V11.py"
V11 - attempt to add semaphore method, so as to recognize the last row before proceed with stepper motor execution
    - this is done via array of dummy angles 888.8 sent from raspberry pi to ESP32, and processed as boolean (round(converter.valueReading[5] * 10) == 8888)
    - Compatible with "Project_Hayley_V4_IK_user_interface_V11.py" 
V12 - Project revamp with updated hardware (new abosolute encoder V2 and new motor controller board - "stepper_with_TMC2209_controller_board_V1")
    - update default values under start_axis_degAngle[no_of_steppers]
    - Compatible with "Project_Hayley_V5_IK_user_interface_V01.py"     
V13 - update default values under start_axis_degAngle[no_of_steppers]
    - add stepper motor disabling logic
    - added I2C to handle different data e.g. angles vs changing stepper mode
    - Compatible with "Project_Hayley_V5_IK_user_interface_V04.py"  
V14 - major revamp to go dual core mode
    - Core 0 → I2C + 6 absolute encoders + target reception from Raspberry Pi
    - Core 1 → 6 stepper motors running AccelStepper + closed-loop PID position control
    - Compatible with "Project_Hayley_V5_IK_user_interface_V04.py"  
V15 - cleanup based on a working V14
    - added "QueueHandle_t jointQueue;" in order to manage stack of back-to-back angle move request from raspberry pi
V16 - create standalone Kp, Ki, Kd constants for each axis
    - Introduce slight speed balancing between the axis motion, pegged to the axis with the longer travel time
    - Compatible with "Project_Hayley_V5_IK_user_interface_V04.py"  
V17 - Introduce servo claw functionality by adding 1 more float data into "union BytesToFloat" 
    - Attempt to split acceptable custom step error/s for each axis, rather than a fixed single value
    - Compatible with "Project_Hayley_V5_IK_user_interface_V05.py"  
V18 - Added magnet_direction[i] to reflect magnet direction. recap motor direction is determined by gear_reduction[x]
    - Modified axis 6 to have correction[x] = error[x]*0.5 rather than PI loop
    - Speed up movement by reducing delay, and remove LERP speed control, for now
    - Compatible with "Project_Hayley_V5_IK_user_interface_V06.py"  
V19 - Cleanup, including fixing USB-serial cannot detect bug 
    - Replaced <AccelStepper.h> with direct register access
    - Compatible with "Project_Hayley_V5_IK_user_interface_V06.py"
V20 - Added ESP-NOW communication protocol for use with PS controller
    - Added safety angle limits motor cut-off
    - Compatible with "Project_Hayley_V5_IK_user_interface_V08.py"

*/

#include <WiFi.h>
#include <esp_now.h>
#include <Wire.h>
//#include <AccelStepper.h>
#include <SPI.h>
#include <algorithm>
#include "driver/mcpwm_prelude.h"

#include "driver/gpio.h"
#include "soc/gpio_struct.h"
#include "esp_task_wdt.h"

/*PINS
   Arduino SPI pins
   MOSI = 11, MISO = 12, SCK = 13, CS = 10
   STM32 SPI pins
   MOSI = PA7, MISO = PA6, SCK = PA5, CS = PA4
   ESP32 SPI pins
   MOSI = 11, MISO = 12, SCK = 13, CS = see below
*/

// START DEFINE SECTION FOR MOTOR CONTROLLER V3
//#define SLAVE_ADDRESS 0x04 // Nano IoT 2
#define SLAVE_ADDRESS 0x05 //ESP32S3

#define MSG_STEPPER_ARRAY 0x01
#define MSG_MODE_STRING   0x02
#define MSG_PS_CONTROLLER 0x03
#define MSG_SPEED         0x04

// Define motor interface type
#define motorInterfaceType 1 //AccelStepper::DRIVER (1) means a stepper driver (with Step and Direction pins)
#define no_of_steppers 6
// #define max_speed 4200 // 2-Jan-26
#define max_speed 20000 // 3-Jan-26
#define motor_acceleration 8000.0 // 2-Jan-26
// #define motor_acceleration 80000.0 // 3-Jan-26

// Define spped for non accelstepper.h method
//#define LAUNCH_SPEED        4000.0f   // 16-Apr-26
//#define FULL_SPEED          32000.0f  // 16-Apr-26
#define LAUNCH_SPEED        1000.0f   // 18-Apr-26
#define FULL_SPEED          1000.0f  // 18-Apr-26
#define LAUNCH_STEPS        0       // 19-Apr-26
#define LAUNCH_INTERVAL_US  ((unsigned long)(1000000.0f / LAUNCH_SPEED))  // 250 µs
#define FULL_INTERVAL_US    ((unsigned long)(1000000.0f / FULL_SPEED))    //  31 µs

#define HIGH_SPEED_RATIO 1.0
#define LOW_SPEED_RATIO 0.2

#define SERVO_GPIO 38 // 20 is actually using USB D+ pin

static float speed_ratio = 1.0;

// ============================================================
//  6-axis independent motor control via ESP-NOW joystick
//  Axis 1 → dpad left(0x08)/right(0x04)
//  Axis 2 → dpad up(0x01)/down(0x02)
//  Axis 3 → lx   (-508 to +512)
//  Axis 4 → ly   (-508 to +512)
//  Axis 5 → rx   (-508 to +512)
//  Axis 6 → ry   (-508 to +512)
// ============================================================

// --- Per-axis independent motion state ---
struct AxisState {
  bool          active;
  bool          forward;
  unsigned long intervalUs;   // µs between steps
  unsigned long lastStepUs;
};

static AxisState axisState[no_of_steppers] = {};

// --- Speed config per axis ---
// Tune these per axis based on load, gear ratio, and feel
const float AXIS_MAX_SPEED[no_of_steppers] = {
  1000.0f,   // Axis 1 — dpad left/right
  1000.0f,   // Axis 2 — dpad up/down
  1000.0f,   // Axis 3 — lx
  1000.0f,   // Axis 4 — ly
  1000.0f,   // Axis 5 — rx
   500.0f,   // Axis 6 — ry (lower — no gearing, gear_reduction = -1)
};

const float AXIS_MIN_SPEED[no_of_steppers] = {
  100.0f,    // Axis 1
  100.0f,    // Axis 2
  100.0f,    // Axis 3
  100.0f,    // Axis 4
  100.0f,    // Axis 5
  100.0f,    // Axis 6
};


// --- Angle limits per axis ---
const int AXIS_MAX_ANGLE[no_of_steppers] = {
  100,   // Axis 1 — dpad left/right
  90,   // Axis 2 — dpad up/down
  90,   // Axis 3 — lx
  120,   // Axis 4 — ly
  100,   // Axis 5 — rx
  179,   // Axis 6 — ry (lower — no gearing, gear_reduction = -1)
};

const int AXIS_MIN_ANGLE[no_of_steppers] = {
  -100,   // Axis 1 — dpad left/right
  -90,   // Axis 2 — dpad up/down
  -90,   // Axis 3 — lx
  -120,   // Axis 4 — ly
  -100,   // Axis 5 — rx
  -179,   // Axis 6 — ry (lower — no gearing, gear_reduction = -1)
};


// Deadzone for analog sticks — values within ±DEADZONE are ignored
#define ANALOG_DEADZONE  30

// // dpad produces fixed speed — no proportional scaling needed
// #define DPAD_SPEED_FAST       600.0f
// #define DPAD_SPEED_SLOW       100.0f

// ============================================================
//  setAxisVelocity() — set speed and direction for one axis
//  speed = 0 stops the axis
// ============================================================

void setAxisVelocity(int axis, float speed, bool forward) {
  if (speed <= 0.0f) {
    axisState[axis].active = false;
    return;
  }
  axisState[axis].intervalUs = (unsigned long)(1000000.0f / (speed*speed_ratio));
  axisState[axis].forward    = forward;
  axisState[axis].active     = true;
}

// ============================================================
//  mapAnalogToSpeed() — maps joystick value to speed
//  input range: -508 to +512
//  deadzone applied, output is always positive (direction separate)
// ============================================================

float mapAnalogToSpeed(int16_t value, float minSpeed, float maxSpeed) {
  if (abs(value) <= ANALOG_DEADZONE) return 0.0f;

  // Normalize to 0.0–1.0 outside deadzone
  float absVal  = abs(value) - ANALOG_DEADZONE;
  float maxVal  = 512.0f - ANALOG_DEADZONE;   // use 512 as positive max
  float ratio   = constrain(absVal / maxVal, 0.0f, 1.0f);

  return minSpeed + ratio * (maxSpeed - minSpeed);
}

mcpwm_cmpr_handle_t comparator;
mcpwm_oper_handle_t oper;
mcpwm_timer_handle_t timer;
mcpwm_gen_handle_t generator;


// ----- PID gains per joint -----
const float Kp[no_of_steppers] = {1.2, 1.2, 1.2, 1.2, 1.2, 0.005}; 
const float Ki[no_of_steppers] = {0.0, 0.0, 0.0, 0.0, 0.0, 0.0}; 
const float Kd[no_of_steppers] = {0.6, 0.6, 0.6, 0.6, 0.6, 0.001}; 

float time_travel[no_of_steppers] = {0.01};
float speed_for_LERP = 25000.0;
volatile long correction[6] = {0};

float integral[no_of_steppers] = {0};
long prevError[no_of_steppers] = {0};
long error[no_of_steppers] = {0};

// ----- Shared feedback data -----
volatile float targetSteps[no_of_steppers];
SemaphoreHandle_t feedbackMutex;

// Motor driver settings
const float micro_steps[no_of_steppers] = {8.0, 8.0, 8.0, 8.0, 8.0, 8.0}; 
//const float micro_steps[no_of_steppers] = {16.0, 16.0, 16.0, 16.0, 16.0, 16.0}; 
const float gear_reduction[no_of_steppers] = {30.0, -30.0, -30.0, 30.0, -30.0, -1.0}; // -ve sign to flip direction of physical motor
const float steps_per_rotation[no_of_steppers] = {200.0, 200.0, 200.0, 200.0, 200.0, 200.0}; 
const int magnet_direction[no_of_steppers] = {-1, 1, 1, -1, 1, 1}; //magnet direction 
const int stepper_pins[no_of_steppers] = {17, 3, 10, 15, 6, 4}; //stepper pin id
const int stepper_direction[no_of_steppers] = {18, 46, 14, 16, 7, 5}; //stepper direction id
const int stepper_enable[no_of_steppers] = {1, 2, 42, 41, 40, 39}; //stepper enable - GND/low to enable
const byte axis_angle_pins[no_of_steppers] = {21, 47, 48, 45, 35, 36}; //CS pins for 6 encoders + 1 spare (sprare is GPIO 36)
//const int steps_error_limit[no_of_steppers] = {40, 40, 40, 40, 40, 8}; // set microstep tolerance limit allow by PID that will mark the target as complete
int steps_error_limit[no_of_steppers] = {10, 10, 10, 10, 10, 2}; // set microstep tolerance limit allow by PID that will mark the target as complete

//  Pin mask table
static uint32_t stepMasks[no_of_steppers];
//static uint32_t allowMasks[no_of_steppers];

// Encoder reading settings
const int windowSize = 5; // Adjust the window size based on your requirements
float sensorValues[no_of_steppers][windowSize];
float axis_degAngle[no_of_steppers] = {0, 0, 0, 0, 0, 0}; //Angle in degrees
float accepted_axis_degAngle[no_of_steppers] = {0, 0, 0, 0, 0, 0}; //Angle in degrees
int currentIndex = 0;
uint16_t rawData = 0; //bits from the encoder (16 bits, but top 2 has to be discarded)
uint16_t command = 0b1111111111111111; //read command (0xFFF)

// use this to find encoder default kinematically zeroed position 
//const float start_axis_degAngle[no_of_steppers] = {0.0, 0.0, 0.0, 0.0, 0.0, 0.0}; //Angle in degrees, encoder values when in kinematic zeroed horizontal position - 3-Oct-25

// kinematically zeroed position 
//const float start_axis_degAngle[no_of_steppers] = {-174.02, 121.2, 91.92, 104.86, 9.30, -3.96}; //Angle in degrees, encoder values when in kinematic zeroed horizontal position - 20-Dec-25 - by estimation only
//const float start_axis_degAngle[no_of_steppers] = {-187.61, 121.91, 92.53, -106.88, 10.89, -4.71}; //Angle in degrees, encoder values when in kinematic zeroed horizontal position - 2-Feb-26 - by using 3 mm pins
const float start_axis_degAngle[no_of_steppers] = {-187.61, 121.91, 92.53, -106.88, 10.89, 116.29}; //Angle in degrees, encoder values when in kinematic zeroed horizontal position - 14-Jun-26 - axis 6 adjust for zero tablet pointer

//define an array of stepper pointers. initialize the pointer to NULL (null pointer) for safety (see below)
//AccelStepper *steppers[no_of_steppers] = {NULL, NULL, NULL, NULL, NULL, NULL};

// Queue handle
QueueHandle_t jointQueue;


// ------------------------------------------------------------
// ESP-NOW PACKET — must match sender struct exactly
// ------------------------------------------------------------
typedef struct __attribute__((packed)) {
  int16_t  lx; // Axis 3
  int16_t  ly; // Axis 4
  int16_t  rx; // Axis 5
  int16_t  ry; // Axis 6
  uint16_t L2; 
  uint16_t R2;
  uint32_t buttons;
  uint8_t  dpad; // Axis 1 - left & right, Axis 2 - up and down
  uint8_t  misc;
} ControllerPacket;

// global state for PS control
volatile bool     espnowActive   = false;  // tracks ESP-NOW on/off
volatile bool     newPacket      = false;  // set true when ESP-NOW data arrives
ControllerPacket  rxData         = {};
volatile unsigned long lastRxTime = 0;
volatile bool     i2cNewCmd      = false;


// https://medium.com/@sandhan.sarma/sending-floats-over-the-i2c-bus-between-two-arduinos-part-2-486db6dc479f
union BytesToFloat {
    // 'converts' incoming bytes to float array, the +1 is for the servo
    byte valueBuffer[(no_of_steppers+1)*8];
    float valueReading[no_of_steppers+1];    
} converter;

// float struct to store angles 
struct __attribute__((packed)) {
  float angles_array[no_of_steppers]; // unit: °
  uint8_t status_flags;               // 1 byte
} encoder; 


//  Per-motor state
struct Motor {
  long absTarget;
  long stepsDone;
  long bresenham;
  bool forward;
};
static Motor motors[no_of_steppers];

//  Active move globals
static volatile bool moveComplete = false;
static volatile bool moveActive   = false;
static volatile long masterSteps  = 0;
static volatile long masterDone   = 0;

//struct motor_steps 
// struct {
//    long steps[no_of_steppers]; // unit: steps
// } motor; 

bool allWithinRange(const long arr[6]) {
    for (int i = 0; i < 6; ++i) {
        if (std::abs(arr[i]) > steps_error_limit[i]) {
            return false;
        }
    }
    return true;
}

// ----- function for motor direction and stepping -----
inline void setDir(int i, bool forward) {
  digitalWrite(stepper_direction[i], forward ? HIGH : LOW);
}

inline void pulseStepMulti(uint32_t mask) {
  if (!mask) return;
  GPIO.out_w1ts = mask;
  delayMicroseconds(1);
  GPIO.out_w1tc = mask;
}

void startMove(long targets[no_of_steppers]) {
  masterSteps = 0;

  for (int i = 0; i < no_of_steppers; i++) {

    //axisState[i].active     = true;

    motors[i].absTarget = abs(targets[i]);
    motors[i].stepsDone = 0;
    motors[i].bresenham = 0;
    motors[i].forward   = (targets[i] >= 0);

    setDir(i, motors[i].forward);

    if (motors[i].absTarget > masterSteps)
      masterSteps = motors[i].absTarget;
  }

  masterDone = 0;
  moveActive = (masterSteps > 0);

  Serial.print("Move started. Master steps: ");
  Serial.println(masterSteps);
}

bool runMove() {
  if (!moveActive) return false;

  static unsigned long lastStepTime = 0;
  unsigned long now = micros();

  bool nearEndpoint = (masterDone < LAUNCH_STEPS) ||
                      ((masterSteps - masterDone) < LAUNCH_STEPS);
  unsigned long interval = nearEndpoint ? LAUNCH_INTERVAL_US : FULL_INTERVAL_US;

  if ((now - lastStepTime) < interval) return true;
  lastStepTime = now;

  masterDone++;

  uint32_t batchMask = 0;
  for (int i = 0; i < no_of_steppers; i++) {
    if (motors[i].stepsDone >= motors[i].absTarget) continue;
    motors[i].bresenham += motors[i].absTarget;
    if (motors[i].bresenham >= masterSteps) {
      motors[i].bresenham -= masterSteps;
      motors[i].stepsDone++;
      batchMask |= stepMasks[i];
    }
  }

  pulseStepMulti(batchMask);

  if (masterDone >= masterSteps) {
    moveActive   = false;
    moveComplete = true;
    // Serial.println removed — Serial inside step loop blocks timing
    return false;
  }

  return true;
}

// ----- function for servo -----
void setServoUs(uint32_t us)
{
  // MCPWM timer resolution = 1 MHz → 1 tick = 1 µs
  mcpwm_comparator_set_compare_value(comparator, us);
}


// ------------------------------------------------------------
// ESP-NOW CALLBACKS
// ------------------------------------------------------------
void onDataRecv(const esp_now_recv_info_t *info,
                const uint8_t *incomingData,
                int len) {
  // Guard: ignore packets if ESP-NOW mode was deactivated mid-flight
  if (!espnowActive) return;

  if (len == sizeof(ControllerPacket)) {
    memcpy(&rxData, incomingData, sizeof(rxData));
    lastRxTime = millis();
    newPacket  = true;  // signal main loop to process

    // Serial.print("LX: "); Serial.print(rxData.lx);
    // Serial.print(" LY: "); Serial.print(rxData.ly);
    // Serial.print(" RX: "); Serial.print(rxData.rx);
    // Serial.print(" RY: "); Serial.println(rxData.ry);
    // Serial.print("L2: "); Serial.print(rxData.L2);
    // Serial.print(" R2: "); Serial.print(rxData.R2);
    // Serial.print(" buttons: "); Serial.println(rxData.buttons, HEX);
    // Serial.print(" dpad: "); Serial.println(rxData.dpad, HEX);
    // Serial.print(" misc: "); Serial.println(rxData.misc, HEX);
    // Serial.print(" BTN: "); Serial.println(rxData.buttons, HEX);

  }
}
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
void loop() {
  vTaskDelay(200); // was 200
}

void receiveData(int byteCount){

  if (byteCount < 2) return;

  uint8_t msgType = Wire.read();
  uint8_t length  = Wire.read();

  switch (msgType) {

    // -----------------------------
    // Stepper motor array
    // -----------------------------
    case MSG_STEPPER_ARRAY: {
      // Serial.println("stepper triggered");
      for(uint8_t index = 0; index<byteCount; index++){
          converter.valueBuffer[index] = Wire.read();
      }
      if (xQueueSend(jointQueue, &converter.valueReading, 0) == pdTRUE) {
        Serial.println("Queued new joint command");
      } else {
        Serial.println("Queue full! Command dropped");
      }
      break;
    }

    // -----------------------------
    // Mode string to enable/disable stepper motors
    // -----------------------------
    case MSG_MODE_STRING: {
    Serial.print("byteCount="); Serial.println(byteCount);
    Serial.print("length byte="); Serial.println(length);
      char mode[32];

      for (int i = 0; i < length && i < 31; i++) {
        mode[i] = Wire.read();
      }
      mode[length] = '\0';

      Serial.print("Mode set to: ");
      Serial.println(mode);

      // Serial.println(strcmp(mode, "enable_stepper"));   

      if (strcmp(mode, "disable_stepper") == 0) {
        // enable disable_stepper mode
        for (int i = 0; i <= (no_of_steppers-1); i++) {
          digitalWrite(stepper_enable[i], HIGH); // Set the pin to HIGH - HIGH to disable
        }
        setStepperEnabled(false);
      }
      else if (strcmp(mode, "enable_stepper") == 0) {
        // enable enable_stepper mode
        for (int i = 0; i <= (no_of_steppers-1); i++) {
          digitalWrite(stepper_enable[i], LOW); // Set the pin to LOW - GND/low to enable
        }
        setStepperEnabled(true);
      }
      break;
    }

    // -----------------------------
    // Mode string to enable/disable PS control
    // -----------------------------
    case MSG_PS_CONTROLLER: {
    Serial.print("byteCount="); Serial.println(byteCount);
    Serial.print("length byte="); Serial.println(length);
      char mode[32];

      for (int i = 0; i < length && i < 31; i++) {
        mode[i] = Wire.read();
      }
      mode[length] = '\0';

      Serial.print("Mode set to: ");
      Serial.println(mode);

      // Serial.println(strcmp(mode, "enable_PS_control"));   

      if (strcmp(mode, "enable_PS_control") == 0) {
        // enable PS_control mode
        Serial.print("Enabling PS control mode");
        startEspNow();
        setPsEnabled(true);
      }
      else if (strcmp(mode, "disable_PS_control") == 0) {
        // disable PS_control mode
        Serial.print("Disabling PS control mode");
        stopEspNow();
        setPsEnabled(false);        
      }
      break;
    }


    // -----------------------------
    // Mode string to toggle motor speed
    // -----------------------------
    case MSG_SPEED: {
    Serial.print("byteCount="); Serial.println(byteCount);
    Serial.print("length byte="); Serial.println(length);
      char mode[32];

      for (int i = 0; i < length && i < 31; i++) {
        mode[i] = Wire.read();
      }
      mode[length] = '\0';

      Serial.print("Mode set to: ");
      Serial.println(mode);

      // Serial.println(strcmp(mode, "enable_PS_control"));   

      if (strcmp(mode, "set_low_speed") == 0) {
        // enable PS_control mode
        Serial.print("Set to low speed");
        speed_ratio = LOW_SPEED_RATIO;

      }
      else if (strcmp(mode, "set_high_speed") == 0) {
        // disable PS_control mode
        Serial.print("Set to high speed");
        speed_ratio = HIGH_SPEED_RATIO;
   
      }
      break;
    }

    default:
    Serial.println("Unknown message type");
  }

}

void setStepperEnabled(bool enabled) {
    if (enabled)
        encoder.status_flags |= (1 << 0);   // set bit 0
    else
        encoder.status_flags &= ~(1 << 0);  // clear bit 0
}

void setPsEnabled(bool enabled) {
    if (enabled)
        encoder.status_flags |= (1 << 1);   // set bit 1
    else
        encoder.status_flags &= ~(1 << 1);  // clear bit 1
}

// test reference from https://stackoverflow.com/questions/40196733/how-to-pass-arduino-struct-to-raspberry-pi-via-i2c
void sendEncoderData(){
  Wire.write((byte *)&encoder, sizeof(encoder)); // 24 bytes floating + 1 = 25 bytes 
}

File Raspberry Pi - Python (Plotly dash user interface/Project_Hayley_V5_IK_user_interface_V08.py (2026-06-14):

# -*- coding: utf-8 -*-
"""
V01 Baseline for Project Hayley V4
V02 Attempt to send encoder data to Pi ==> success with "Project_Hayley_ESP32_V3.ino" 
V03 Attempt to convert encoder data from long to float and tabulate in dash table with new table id "encoder_position_table"
V04 Add homing capability ==> success with "Project_Hayley_ESP32_V4.ino" 
V05 Working baseline as of 7-May-25
V06 Update with actual physical linkage for Hayley V4. Attempt to add in box entry for fine stepper movement 
    Compaitible with "Project_Hayley_ESP32_V5.ino"
V07 Update to box entry for angles entry for FK
    Update kinematics movement calculations to use with "return_encoder = get_encoder_data()"
    This is make movements base on actual encoder readings before movement - this version do not make use of feedback loop yet
    Compaitible with "Project_Hayley_ESP32_V5.ino"
    Compaitible with "Project_Hayley_ESP32_V6.ino"
    Compaitible with "Project_Hayley_ESP32_V7.ino"

V08 Correct homing logic for encoders based. Remove calibration button (calibration shall be done after home with BNO055)
    Removed Project Hayley V3 data
    optimize DH_matrix e.g. let all theta/180*np.pi be theta_rad
    
V09 major change attempt to switch steps calculation from python/raspberry side to ESP32
    get_encoder_data() updated to process incoming data as float instead of long datatype
    function call change from "writeNumbers(steps)" to "writeAngles(angles_list)"
    Compaitible with "Project_Hayley_ESP32_V9.ino" 

V10 Update interface to have both angular and steps display on same main page
    removed callback "update_stpper_position_div(btn4)" and attempt to add auto update of encoder data instead
    Compaitible with "Project_Hayley_ESP32_V9.ino" 
    
V11 Remove function "Inverse_Kinematics_CCD" as the focus is on raspberry Pi to function as user interface
    The IK solver should remain on a PC 

V12 Cleanup   
    Update step page to reflect absolute stepper position (steps) after each travel
    Removed method of 'Cubic Polynomial' and 'Quintic Polynomial'as this should be part of the IK solver seperately
    

V03 added auto-retrieval of encoder data every 5 sec
    added stepper motor disabling logic
    added I2C to handle different data e.g. angles vs changing stepper mode
    Compaitible with "Project_Hayley_ESP32_V13.ino" 

V04 add capability to record robot arm positions (disable motor), save to csv for repeat later 
    Compaitible with "Project_Hayley_ESP32_V14.ino" 
    Compaitible with "Project_Hayley_ESP32_V15.ino" 
    Compaitible with "Project_Hayley_ESP32_V16.ino" 
    
V05 added byte msg for servo commmands
    added servo function "writeAngles_servo" to replace "writeAngles"
    Basically 0.0 == claw open, 1.0 == claw close and other values == do nothing
    Compaitible with "Project_Hayley_ESP32_V17.ino" 
    
V06 updated linkage values in local_linkage_data
    Remove the update values in dcc.input, defaulting to "none", as the encoder data are now updated every second now
    Compaitible with "Project_Hayley_ESP32_V18.ino" 
    
V07 Add a mode for direct PS controller to system ESP32-S3 via ESP-NOW 
    Compaitible with "Project_Hayley_ESP32_V20.ino" 
    
V08 Add PS control option on recording page
    Update for better web layout
    Compaitible with "Project_Hayley_ESP32_V20.ino" 
    
Features to be added
multi angle calibration capability

"""

import dash
from dash import Dash, dcc, html, Output, Input
import plotly.express as px
import plotly.graph_objs as go
import pandas as pd
import numpy as np
import smbus2 as smbus
import struct
import time
import math
from skspatial.objects import Plane, Point, Vector
import base64
import io
from dash import dash_table
import dash_bootstrap_components as dbc
import subprocess
from dash_extensions.enrich import Output, DashProxy, Input, MultiplexerTransform
from dash.exceptions import PreventUpdate
from datetime import datetime
import math
from math import (
    asin, pi, atan2, cos 
)

# device address
arduino_IOT = 0x04
ESP32_IOT = 0x05

# Message type constants
MSG_STEPPER_ARRAY = 0x01 # define mode to send angles over I2C 
MSG_MODE_STRING   = 0x02 # define mode to send stepper mode over I2C
MSG_PS_CONTROLLER   = 0x03 # define mode to send PS controller mode over I2C
MSG_SPEED   = 0x04 # define mode to send speed mode over I2C

# initialize serial commumication
bus = smbus.SMBus(1)
time.sleep(1)

angle_slider_resolution = 0.1 # degrees


gear_reduction = [-30, -30, -30, 30, -30, -1] #-ve sign to flip direction of physical motor
steps_per_rotation = [200, 200, 200, 200, 200, 200]
micro_steps = [8, 8, 8, 8, 8, 8]

hinge_length = 14 # for illustrating the axis hinge in 3d view
max_iter = 500 # iterations allow for IK CCD
err_min = 2.5 # acceptable error in mm in inverse kinematics calculation

figure_axis_limit = 500

# config file to limit the max min angles of the axis
config_df = pd.read_csv('config - project Hayley V5.csv')
lower_limit = list(config_df["Absolute low angle limit"])
upper_limit = list(config_df["Absolute high angle limit"])


# angle_lower_limit = list(np.round((np.array(lower_limit) + 180) % 360 - 180,0))   
# angle_upper_limit = list(np.round((np.array(upper_limit) + 180) % 360 - 180,0))   

angle_lower_limit = lower_limit  
angle_upper_limit = upper_limit


start_angles_list = list(config_df["Start angle"])
angles_list = start_angles_list.copy()

list_of_thetas = [0] * 32 # To be updated

index_of_angles = [2, 8, 11, 18, 26, 30] #hinge for project Hayley v4
index_of_hinges = index_of_angles.copy()

angle_max = list_of_thetas.copy()
angle_min = list_of_thetas.copy()
list_of_blockers = list_of_thetas.copy()
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

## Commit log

2025-09-02 Initial Upload
    Initial upload for sub-system test: 1 stepper + 1 encoder
2025-10-05 Uploading PCBA project files
    KiCAD files - both absolute encoder as well as the motor controller adaptor board
    [Rotary_Encoder_AS5048A_V8-B_Cu.gbr, Rotary_Encoder_AS5048A_V8-B_Mask.gbr, Rotary_Encoder_AS5048A_V8-B_Paste.gbr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]
2025-10-13 CAD upload
    Step files and drawings done in OnShape
    [Part Studio 23.step, Part Studio 28.step, Part Studio 29.step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]
2025-12-16 Raspberry Pi hosted GUI
    Python based - plotly dash.
    [config - project Hayley V5.csv]
2025-12-24 Update to enable/disable stepper motor
2025-12-31 Significant updates to both codes on raspberry Pi and ESP32
    ESP32 update to operate in dual core mode and also the ability to disable the stepper motor drivers, so as to manipulate the positions of arms. Also added CSV recording ability (learning capability)
    Project_Hayley_V5_IK_user_interface_V04.py
    V04 add capability to record robot arm positions (disable motor), save to csv for repeat later
    Compaitible with "Project_Hayley_ESP32_V14.ino"
    Project_Hayley_ESP32_V14.ino
    V14 - major revamp to go dual core mode
    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
2026-01-04 Create Project_Hayley_ESP32_V15.ino
    Project_Hayley_ESP32_V15 - added "QueueHandle_t jointQueue;" in order to manage stack of back-to-back angle move request from raspberry pi. Can handle 100 queue at once.
2026-01-21 servo basic check
    subsystem: servo sanity check
2026-01-23 Added servo function
    Servo function added in "Project_Hayley_V5_IK_user_interface_V05.py" and "Project_Hayley_ESP32_V17.ino"
2026-02-02 General update
    General updates as indicated in history - but more important one is regarding the accounting of magnet encoder direction.
2026-04-26 Create Project_Hayley_ESP32_V20.ino
    Interim update for V20
    V20 - Added ESP-NOW communication protocol for use with PS controller
    - Added safety angle limits motor cut-off
    - Compatible with "Project_Hayley_V5_IK_user_interface_V07.py"
2026-05-03 Checkpoint update
    Update, before cleanup.
    ESP32-DevKitC-1 (N16R8) -
    Project_Hayley_ESP32_V20.ino
    Raspberry Pi 3B and above -
    Project_Hayley_V5_IK_user_interface_V08.py
    DOIT ESP32 DEVKIT V1 -
    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
2026-06-14 Update for PS controller bug
    [Project_Hayley_ESP32_V20.ino, Project_Hayley_V5_IK_user_interface_V08.py]
